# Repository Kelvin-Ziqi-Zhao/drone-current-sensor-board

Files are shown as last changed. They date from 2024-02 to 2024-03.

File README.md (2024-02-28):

# Drone Current Sensor Board
High current sensor board for battery+capacitor power supply system.
[Lastest releases](https://github.com/Kelvin-Ziqi-Zhao/drone-current-sensor-board/releases/latest)
## Components and Design
- Use **RP2040** as MCU, **INA226** as power monitor chip.
- By using **0402** components, the size of module can be greatly reduced
## More Info
- DEBUG, UART test points and IIC select are reserved, which could help us during development
- This is the theory verification PCBA module of my follow-up power system, stay tuned...
>The hardware isn't been tested, please **CHECK THE CIRCUIT** before power-on




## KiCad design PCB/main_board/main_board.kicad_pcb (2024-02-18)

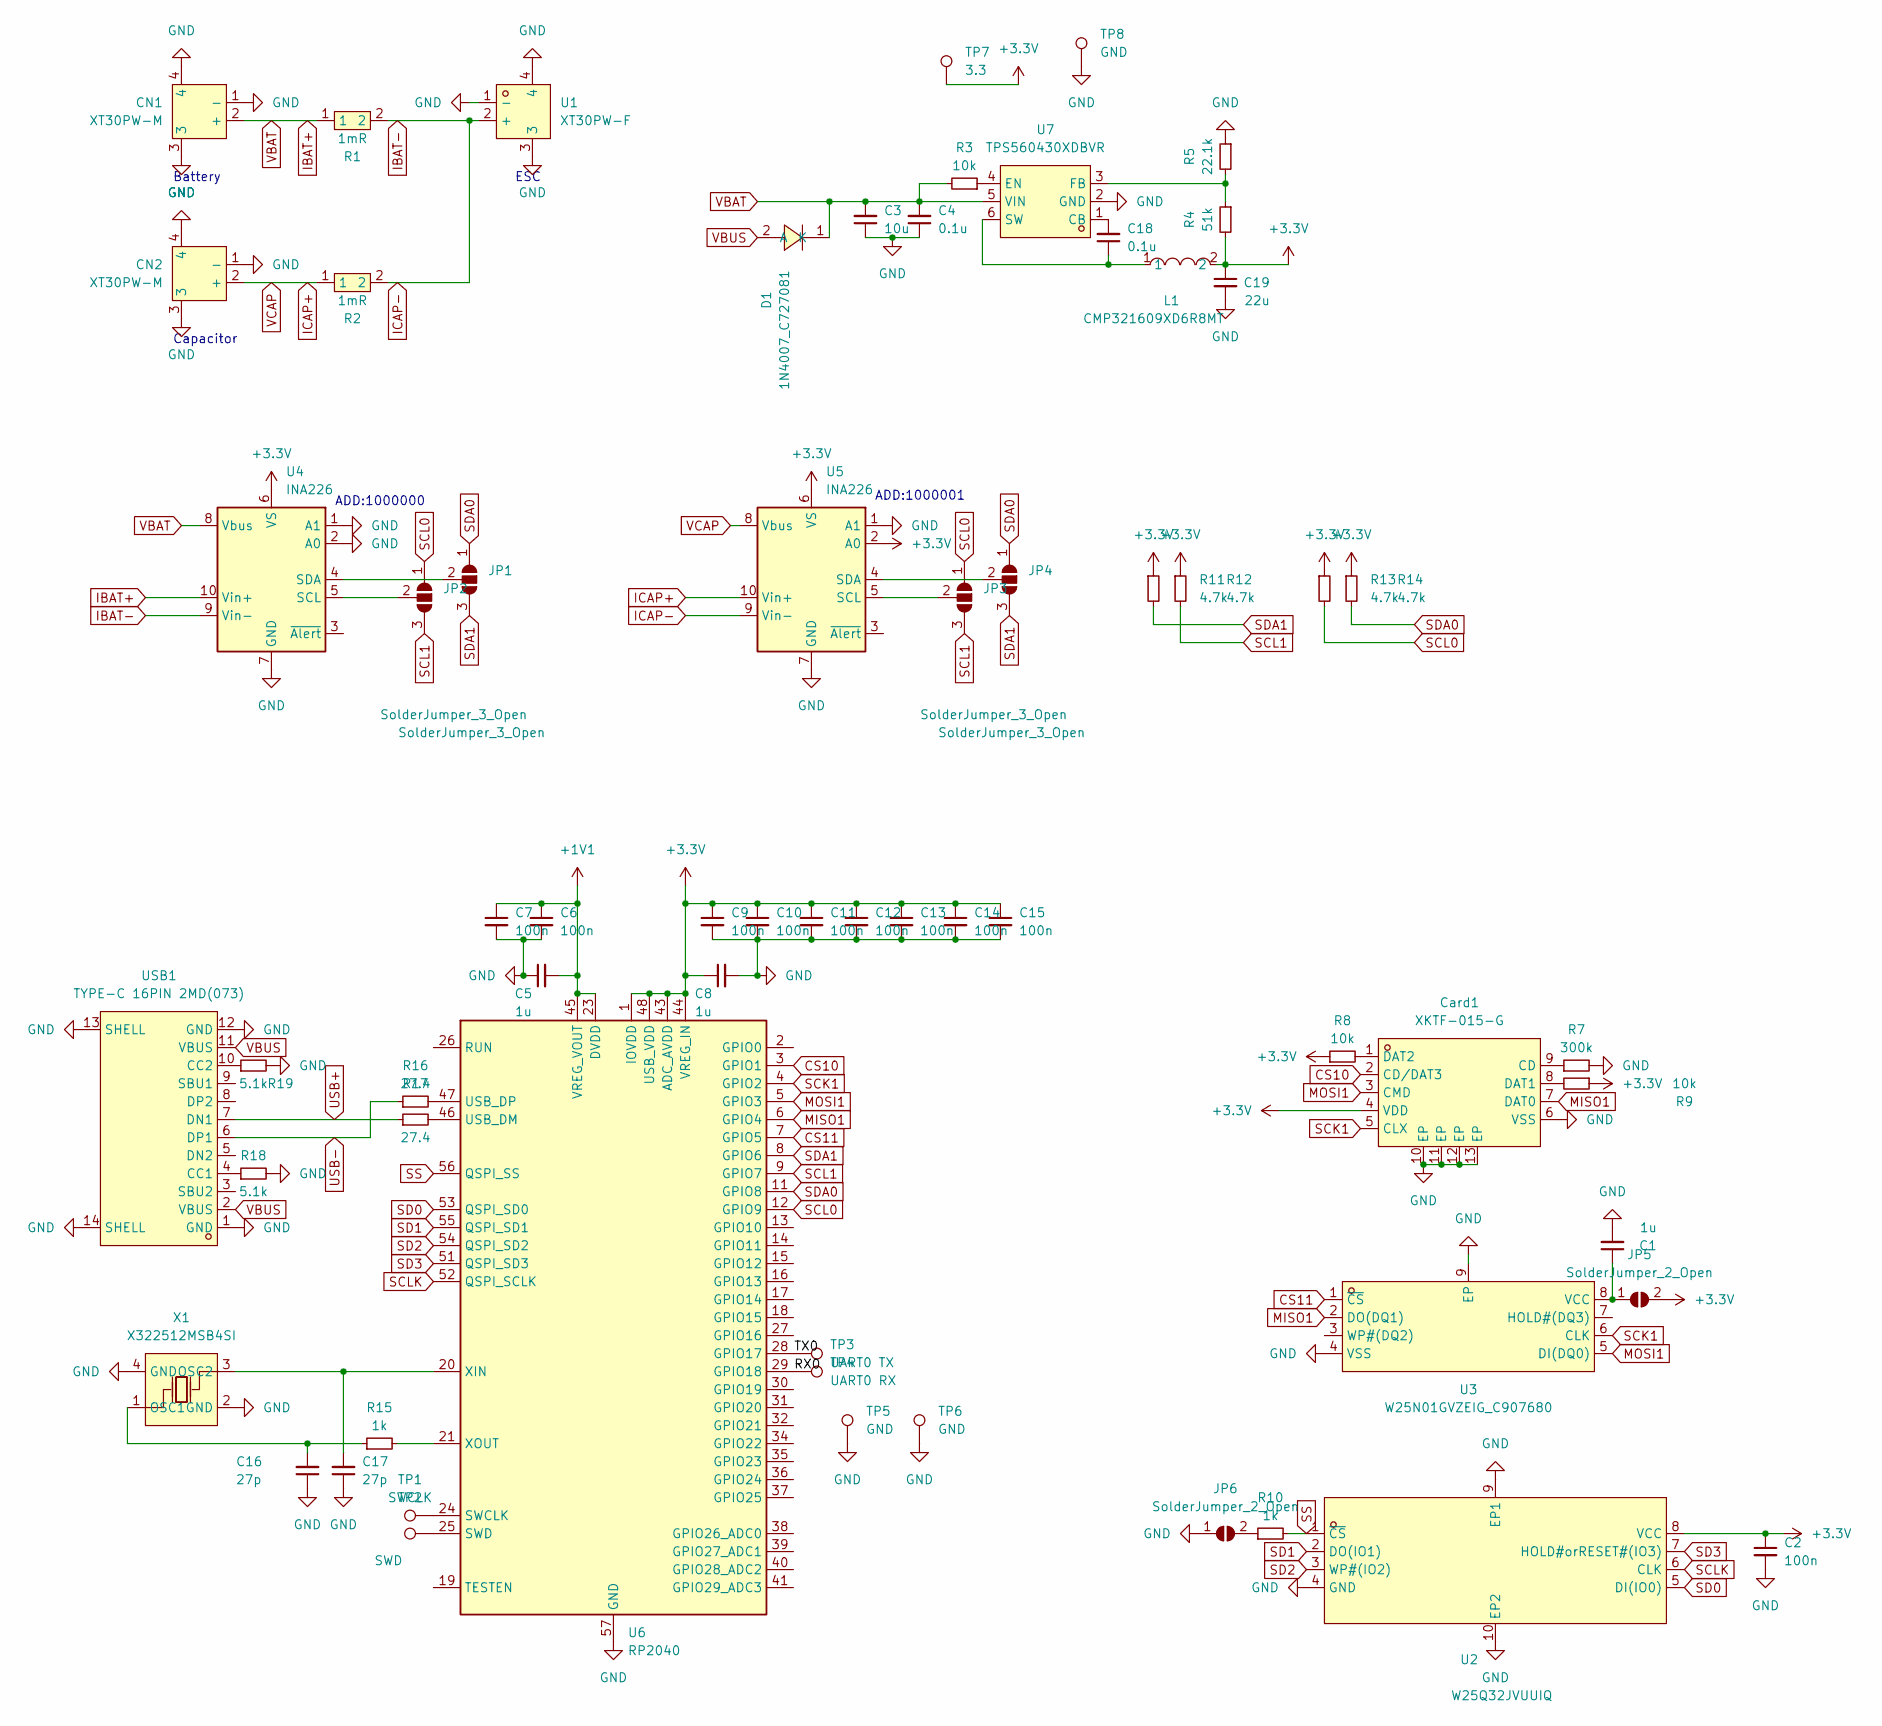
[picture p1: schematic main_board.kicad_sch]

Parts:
C1, C5, C8: 1u; C_0402_1005Metric
C2, C6, C7, C9, C10, C11, C12, C13, C14, C15: 100n; C_0402_1005Metric
C3: 10u; C_0603_1608Metric
C4: 0.1u; C_0603_1608Metric
C16, C17: 27p; C_0402_1005Metric
C18: 0.1u; C_0402_1005Metric
C19: 22u; C_0805_2012Metric
CN1, CN2: XT30PW-M; CONN-TH_XT30PW-M; LCSC Part C431092
Card1: XKTF-015-G; TF-SMD_XKTF-015-N; LCSC Part C1121874
D1: 1N4007_C727081; SMA_L4.3-W2.5-LS5.0-RD; LCSC Part C727081
JP1, JP2, JP3, JP4: SolderJumper_3_Open; SolderJumper-3_P1.3mm_Open_Pad1.0x1.5mm
JP5, JP6: SolderJumper_2_Open; SolderJumper-2_P1.3mm_Open_Pad1.0x1.5mm
L1: CMP321609XD6R8MT; L1206; LCSC Part C395031
R1, R2: 1mR; R3920; LCSC Part C5224161
R3: 10k; C_0402_1005Metric
R4: 51k; C_0402_1005Metric
R5: 22.1k; C_0402_1005Metric
R7: 300k; R_0402_1005Metric
R8, R9: 10k; R_0402_1005Metric
R10, R15: 1k; R_0402_1005Metric
R11, R12, R13, R14: 4.7k; R_0402_1005Metric
R16, R17: 27.4; R_0402_1005Metric
R18, R19: 5.1k; R_0402_1005Metric
TP1: SWCLK; TestPoint_Pad_1.5x1.5mm
TP2: SWD; TestPoint_Pad_1.5x1.5mm
TP3: UART0 TX; TestPoint_Pad_1.5x1.5mm
TP4: UART0 RX; TestPoint_Pad_1.5x1.5mm
TP5, TP6, TP8: GND; TestPoint_Pad_1.5x1.5mm
TP7: 3.3; TestPoint_Pad_1.5x1.5mm
U1: XT30PW-F; CONN-TH_XT30PW-F-1; LCSC Part C2913282
U2: W25Q32JVUUIQ; USON-8_L4.0-W3.0-P0.80-BL_WINBOND_UU; LCSC Part C2999380
U3: W25N01GVZEIG_C907680; WSON-8_L8.0-W6.10-P1.27-BL-EP; LCSC Part C907680
U4, U5: INA226; MSOP-10_L3.0-W3.0-P0.50-LS5.0-BL
U6: RP2040; QFN-56-1EP_7x7mm_P0.4mm_EP3.2x3.2mm
U7: TPS560430XDBVR; SOT-23-6_L2.9-W1.6-P0.95-LS2.8-BL; LCSC Part C524782
USB1: TYPE-C 16PIN 2MD(073); USB-C-SMD_TYPE-C-6PIN-2MD-073; LCSC Part C2765186
X1: X322512MSB4SI; OSC-SMD_4P-L3.2-W2.5-BL; LCSC Part C9002

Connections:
+1V1: C5.2, C6.1, C7.1, U6.23 (DVDD), U6.45 (VREG_VOUT), U6.50 (DVDD)
/RX0: TP4.1, U6.29 (GPIO18)
/TX0: TP3.1, U6.28 (GPIO17)
CS10: Card1.2 (CD/DAT3), U6.3 (GPIO1)
CS11: U3.1 (~CS), U6.7 (GPIO5)
IBAT-: R1.2, R2.2, U1.2 (+), U4.9 (Vin-), U5.9 (Vin-)
ICAP+: CN2.2 (+), R2.1, U5.8 (Vbus), U5.10 (Vin+)
MISO1: Card1.7 (DAT0), U3.2 (DO(DQ1)), U6.6 (GPIO4)
MOSI1: Card1.3 (CMD), U3.5 (DI(DQ0)), U6.5 (GPIO3)
unnamed: Card1.9 (CD), R7.1
unnamed: Card1.8 (DAT1), R9.2
unnamed: Card1.1 (DAT2), R8.2
unnamed: JP1.2 (C), U4.4 (SDA)
unnamed: JP2.2 (C), U4.5 (SCL)
unnamed: JP3.2 (C), U5.5 (SCL)
unnamed: JP4.2 (C), U5.4 (SDA)
unnamed: C1.1, JP5.1 (A), U3.8 (VCC)
unnamed: JP6.2 (B), R10.1
unnamed: TP1.1, U6.24 (SWCLK)
unnamed: TP2.1, U6.25 (SWD)
unnamed: R17.2, U6.46 (USB_DM)
unnamed: R16.2, U6.47 (USB_DP)
unnamed: C17.2, U6.20 (XIN), X1.3 (OSC2)
unnamed: R15.2, U6.21 (XOUT)
unnamed: C18.2, U7.1 (CB)
unnamed: R3.1, U7.4 (EN)
unnamed: R4.1, R5.2, U7.3 (FB)
unnamed: C18.1, L1.1, U7.6 (SW)
unnamed: R18.1, USB1.4 (CC1)
unnamed: R19.1, USB1.10 (CC2)
unnamed: C16.2, R15.1, X1.1 (OSC1)
SCK1: Card1.5 (CLX), U3.6 (CLK), U6.4 (GPIO2)
SCL0: JP2.1 (A), JP3.1 (A), R13.2, U6.12 (GPIO9)
SCL1: JP2.3 (B), JP3.3 (B), R12.2, U6.9 (GPIO7)
SCLK: U2.6 (CLK), U6.52 (QSPI_SCLK)
SD0: U2.5 (DI(IO0)), U6.53 (QSPI_SD0)
SD1: U2.2 (DO(IO1)), U6.55 (QSPI_SD1)
SD2: U2.3 (WP#(IO2)), U6.54 (QSPI_SD2)
SD3: U2.7 (HOLD#orRESET#(IO3)), U6.51 (QSPI_SD3)
SDA0: JP1.1 (A), JP4.1 (A), R14.2, U6.11 (GPIO8)
SDA1: JP1.3 (B), JP4.3 (B), R11.2, U6.8 (GPIO6)
SS: R10.2, U2.1 (~CS), U6.56 (QSPI_SS)
USB+: R17.1, USB1.7 (DN1)
USB-: R16.1, USB1.6 (DP1)
VBUS: D1.2 (A), USB1.2 (VBUS), USB1.11 (VBUS)

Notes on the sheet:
ADD:1000001
ESC
ADD:1000000
Battery
Capacitor

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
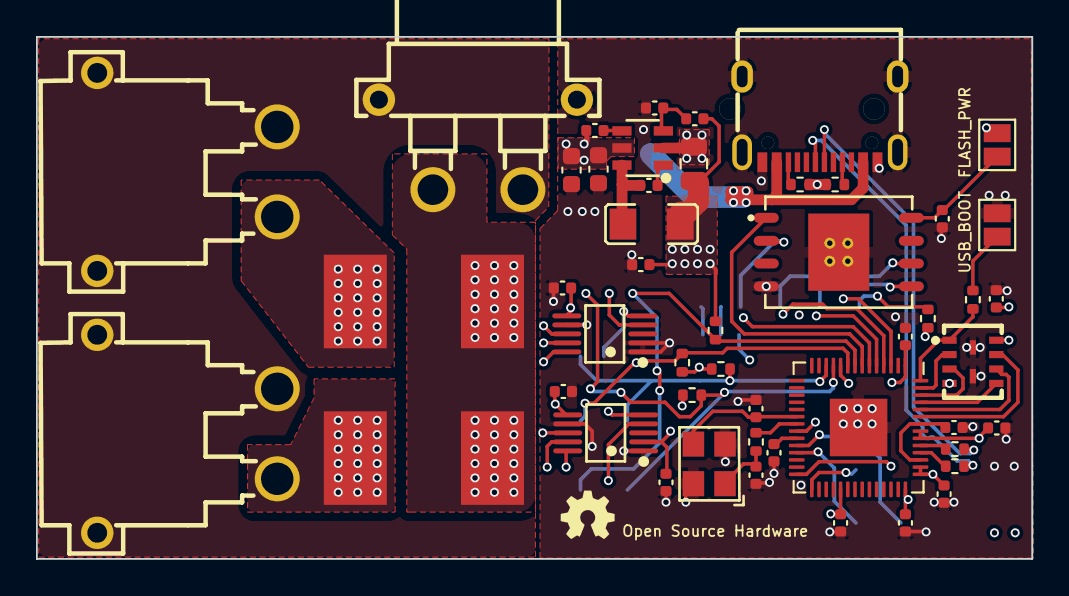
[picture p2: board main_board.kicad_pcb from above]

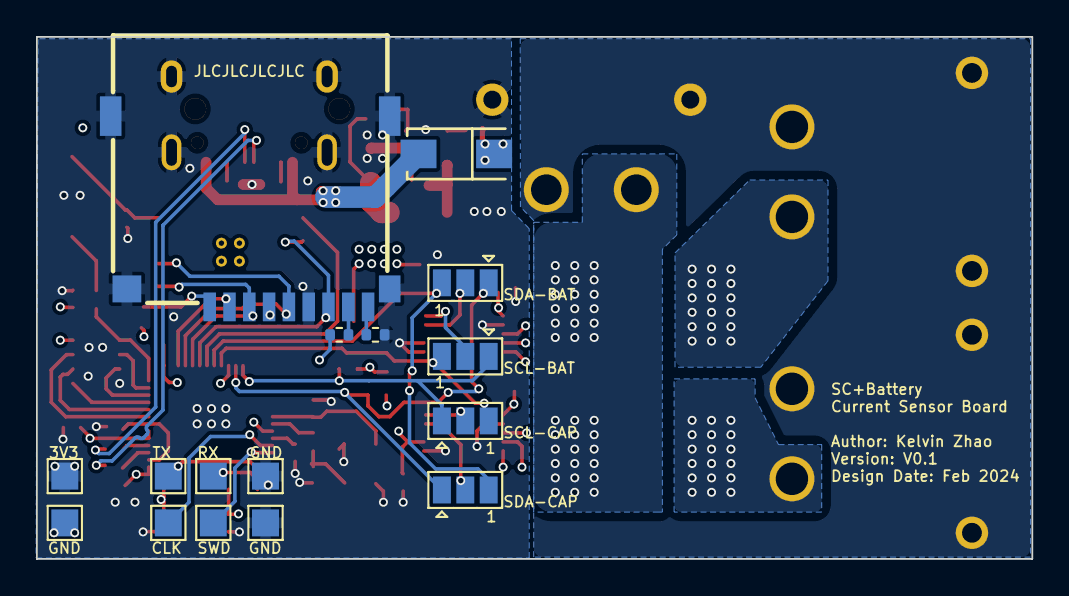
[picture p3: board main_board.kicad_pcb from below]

Board: 4 copper layers, 55.3 x 29.0 mm, 65 parts (16 on the bottom side), 48 nets.

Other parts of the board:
C4#2: 0.1u; C_0603_1608Metric

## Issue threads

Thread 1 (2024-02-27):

Wrong USB2.0 series resistance

Kelvin-Ziqi-Zhao, 2024-02-27:
The schematic and PCB design label the series resistance of 27.4R. But due to a selection mistake, a 27kR resistance has been SMT on that place. I short the wire to skip that resistance, finally it works
**SMT-BOM change required** [bom.xls](https://github.com/Kelvin-Ziqi-Zhao/drone-current-sensor-board/files/14421705/bom.xls)
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

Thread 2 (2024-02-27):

The label of 3V3 and GND test points are reversed

Kelvin-Ziqi-Zhao, 2024-02-27:
On the lower left corner (back skillscreen), the label is wrong
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

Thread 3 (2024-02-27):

Wrong UART0 pinout

Kelvin-Ziqi-Zhao, 2024-02-27:
Ref to official data sheet,  the correct UART pair is GP16-TX, GP17-RX. But in my design, I map it to GP17, GP18 :(
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

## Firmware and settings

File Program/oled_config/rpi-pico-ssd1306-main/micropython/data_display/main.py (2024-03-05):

###############################################################
# SSD1306 OLED Display I2C Tests with the Raspberry Pi Pico
# -- ADC Reading and Display of MEMS Microphone
#
# by Joshua Hrisko, Maker Portal LLC (c) 2021
#
#
# Based on the Pico Micropython repository at:
# https://github.com/raspberrypi/pico-micropython-examples/tree/master/i2c/1306oled
###############################################################
#
#
from machine import Pin, I2C, ADC
from ssd1306 import SSD1306_I2C
import framebuf,sys,time

pix_res_x  = 128 # SSD1306 horizontal resolution
pix_res_y = 64   # SSD1306 vertical resolution

i2c_dev = I2C(1,scl=Pin(7),sda=Pin(6),freq=200000)  # start I2C on I2C1 (GPIO 26/27)
i2c_addr = [hex(ii) for ii in i2c_dev.scan()] # get I2C address in hex format
if i2c_addr==[]:
    print('No I2C Display Found') 
    sys.exit() # exit routine if no dev found
else:
    print("I2C Address      : {}".format(i2c_addr[0])) # I2C device address
    print("I2C Configuration: {}".format(i2c_dev)) # print I2C params


oled = SSD1306_I2C(pix_res_x, pix_res_y, i2c_dev) # oled controller

oled.write_cmd(0xc0) # flip display to place 0,0 at lower-left corner
adc_2 = machine.ADC(2) # ADC channel 2 for input
while True:
    oled.fill(0) # clear the display
    for jj in range(pix_res_x): # loop through horizontal display resolution
        adc_pt = adc_2.read_u16() # read adc and get 16-bit data point
        plot_pt = (adc_pt/((2**16)-1))*(pix_res_y-1) # convert to OLED pixels
        oled.text('.',jj,int(plot_pt)) # update x=jj with data point
    oled.show() # show the new text and image

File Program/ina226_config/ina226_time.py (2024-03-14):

# The MIT License (MIT)
#
# Copyright (c) 2017 Dean Miller for Adafruit Industries
# Copyright (c) 2020 Christian Becker
#
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
# THE SOFTWARE IS PROVIDED "AS IS", WITHOUT WARRANTY OF ANY KIND, EXPRESS OR
# IMPLIED, INCLUDING BUT NOT LIMITED TO THE WARRANTIES OF MERCHANTABILITY,
# FITNESS FOR A PARTICULAR PURPOSE AND NONINFRINGEMENT. IN NO EVENT SHALL THE
# AUTHORS OR COPYRIGHT HOLDERS BE LIABLE FOR ANY CLAIM, DAMAGES OR OTHER
# LIABILITY, WHETHER IN AN ACTION OF CONTRACT, TORT OR OTHERWISE, ARISING FROM,
# OUT OF OR IN CONNECTION WITH THE SOFTWARE OR THE USE OR OTHER DEALINGS IN
# THE SOFTWARE.
# Edit by Kelvin Zhao
"""
`ina226`
====================================================

micropython driver for the INA226 current sensor.

* Author(s): Christian Becker

"""
# taken from https://github.com/robert-hh/INA219 , modified for the INA226 devices by
# Christian Becker
# June 2020

from micropython import const
# from adafruit_bus_device.i2c_device import I2CDevice

__version__ = "0.0.0-auto.0"
__repo__ = "https://github.com/elschopi/TI_INA226_micropython.git"

# Bits
# pylint: disable=bad-whitespace
_READ = const(0x01)

# Config Register (R/W)
_REG_CONFIG = const(0x00)
_CONFIG_RESET = const(0x8000)  # Reset Bit
# Constant bits - don't change
_CONFIG_CONST_BITS = const(0x4000)
# Averaging mode
_CONFIG_AVGMODE_MASK = const(0x0e00)
_CONFIG_AVGMODE_1SAMPLES = const(0x0000)
_CONFIG_AVGMODE_4SAMPLES = const(0x0200)
_CONFIG_AVGMODE_16SAMPLES = const(0x0400)
_CONFIG_AVGMODE_64SAMPLES = const(0x0600)
_CONFIG_AVGMODE_128SAMPLES = const(0x0800)
_CONFIG_AVGMODE_256SAMPLES = const(0x0a00)
_CONFIG_AVGMODE_512SAMPLES = const(0x0c00)
_CONFIG_AVGMODE_1024SAMPLES = const(0x0e00)

# Bus voltage conversion time
_CONFIG_VBUSCT_MASK = const(0x01c0)
_CONFIG_VBUSCT_140us = const(0x0000)
_CONFIG_VBUSCT_204us = const(0x0040)
_CONFIG_VBUSCT_332us = const(0x0080)
_CONFIG_VBUSCT_588us = const(0x00c0)
_CONFIG_VBUSCT_1100us = const(0x0100)
_CONFIG_VBUSCT_21116us = const(0x0140)
_CONFIG_VBUSCT_4156us = const(0x0180)
_CONFIG_AVGMODE_8244us = const(0x01c0)

# Shunt voltage conversion time
_CONFIG_VSHUNTCT_MASK = const(0x0038)
_CONFIG_VSHUNTCT_140us = const(0x0000)
_CONFIG_VSHUNTCT_204us = const(0x0008)
_CONFIG_VSHUNTCT_332us = const(0x0010)
_CONFIG_VSHUNTCT_588us = const(0x0018)
_CONFIG_VSHUNTCT_1100us = const(0x0020)
_CONFIG_VSHUNTCT_21116us = const(0x0028)
_CONFIG_VSHUNTCT_4156us = const(0x0030)
_CONFIG_VSHUNTCT_8244us = const(0x0038)

# Operating mode
_CONFIG_MODE_MASK = const(0x0007)  # Operating Mode Mask
_CONFIG_MODE_POWERDOWN = const(0x0000)
_CONFIG_MODE_SVOLT_TRIGGERED = const(0x0001)
_CONFIG_MODE_BVOLT_TRIGGERED = const(0x0002)
_CONFIG_MODE_SANDBVOLT_TRIGGERED = const(0x0003)
_CONFIG_MODE_ADCOFF = const(0x0004)
_CONFIG_MODE_SVOLT_CONTINUOUS = const(0x0005)
_CONFIG_MODE_BVOLT_CONTINUOUS = const(0x0006)
_CONFIG_MODE_SANDBVOLT_CONTINUOUS = const(0x0007)

# SHUNT VOLTAGE REGISTER (R)
_REG_SHUNTVOLTAGE = const(0x01)

# BUS VOLTAGE REGISTER (R)
_REG_BUSVOLTAGE = const(0x02)

# POWER REGISTER (R)
_REG_POWER = const(0x03)

# CURRENT REGISTER (R)
_REG_CURRENT = const(0x04)

# CALIBRATION REGISTER (R/W)
_REG_CALIBRATION = const(0x05)
# pylint: enable=bad-whitespace


def _to_signed(num):
    if num > 0x7FFF:
        num -= 0x10000
    return num


class INA226:
    """Driver for the INA226 current sensor"""
    def __init__(self, i2c_device, addr=0x40):
        self.i2c_device = i2c_device

        self.i2c_addr = addr
        self.buf = bytearray(2)
        # Multiplier in mA used to determine current from raw reading
        self._current_lsb = 0
        # Multiplier in W used to determine power from raw reading
        self._power_lsb = 0

        # Set chip to known config values to start
        self._cal_value = 4096
        self.set_calibration()

    def _write_register(self, reg, value):
        self.buf[0] = (value >> 8) & 0xFF
        self.buf[1] = value & 0xFF
        self.i2c_device.writeto_mem(self.i2c_addr, reg, self.buf)

    def _read_register(self, reg):
        self.i2c_device.readfrom_mem_into(self.i2c_addr, reg & 0xff, self.buf)
        value = (self.buf[0] << 8) | (self.buf[1])
        return value

    @property
    def shunt_voltage(self):
        """The shunt voltage (between V+ and V-) in Volts (so +-.327V)"""
        value = _to_signed(self._read_register(_REG_SHUNTVOLTAGE))
        # The least signficant bit is 10uV which is 0.00001 volts
        return value * 0.01 /4

    @property
    def bus_voltage(self):
        """The bus voltage (between V- and GND) in Volts"""
        raw_voltage = self._read_register(_REG_BUSVOLTAGE)
        # voltage in millVolt is register content multiplied with 1.25mV/bit
        voltage_mv = raw_voltage * 1.25
        # Return Volts instead of milliVolts
        return voltage_mv * 0.001

    @property
    def current(self):
        """The current through the shunt resistor in milliamps."""
        # Sometimes a sharp load will reset the INA219, which will
        # reset the cal register, meaning CURRENT and POWER will
        # not be available ... athis by always setting a cal
        # value even if it's an unfortunate extra step
        self._write_register(_REG_CALIBRATION, self._cal_value)

        # Now we can safely read the CURRENT register!
        raw_current = _to_signed(self._read_register(_REG_CURRENT))
        return raw_current * self._current_lsb
    
    @property
    def power(self):
        # INA226 stores the calculated power in this register        
        raw_power = _to_signed(self._read_register(_REG_POWER))
        # Calculated power is derived by multiplying raw power value with the power LSB
        return raw_power * self._power_lsb
# Example calculations for calibration register value, current LSB and power LSB
# 1. Assuming a 100milliOhm resistor as shunt
# RSHUNT = 0.1
#
# 2. Determine current_lsb
# Assuming a maximum expected current of 3.6A
# current_lsb = MaxExpected_I / (2^15)
# current_lsb = 3.6A / (2^15)
# current_lsb = 0.0001098632813
# -> Rounding to "nicer" numbers:
# current_lsb = 0.0001
#
# 3. Setting the power LSB
# power_lsb = 25 * current_lsb
# power_lsb = 25 * 0.0001
# power_lsb = 0.0025
#
# 4. Determine calibration register value
# cal_value = 0.00512 / (RSHUNT * current_lsb)
# cal_value = 0.00512 / (0.1 * 0.0001)
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

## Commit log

2024-02-12 Local file update
    [main_board.kicad_pcb, main_board.kicad_sch]
2024-02-12 Create pcb layout
    [main_board.kicad_pcb]
2024-02-12 Fundamental pcb layout
    [main_board.kicad_pcb]
2024-02-12 Change INA226 connection
    [main_board.kicad_sch]
2024-02-12 add PCB outline, redesign power component
    [main_board.kicad_pcb]
2024-02-12 basic layout complete
    [main_board.kicad_pcb]
2024-02-12 stage pull
    [main_board.kicad_pcb]
2024-02-13 Change lib to relative path
    [main_board.kicad_pcb]
2024-02-14 Add EEPROM to mcu; Change R and C to 0402
    [main_board.kicad_pcb, main_board.kicad_sch]
2024-02-14 Fundamental layout complete
    [main_board.kicad_pcb]
2024-02-14 Change IIC0, IIC1 and SPI connection GPIO
    [main_board.kicad_pcb, main_board.kicad_sch]
2024-02-14 Complete SPI Flash and part of decouple capacitor layout
    [main_board.kicad_pcb, main_board.kicad_sch]
2024-02-14 Complete INA226 IIC trace
    [main_board.kicad_pcb]
2024-02-14 Complete high current trace
    [main_board.kicad_pcb, main_board.kicad_sch]
2024-02-14 Complete VBUS trace; Adjust Flash position
    [main_board.kicad_pcb]
2024-02-16 Complete USB DP routing
    [main_board.kicad_pcb, main_board.kicad_sch]
2024-02-16 PCB route complete
    [main_board.kicad_pcb]
2024-02-16 Optimize ref to DCR
    [main_board.kicad_pcb]
2024-02-16 DRC Check complete
    [main_board.kicad_pcb]
2024-02-16 Place text for test point; Disconnect a ground error connection
    [main_board.kicad_pcb, main_board_bom.csv]
2024-02-16 Thicker the single ground connection
    [main_board.kicad_pcb]
2024-02-16 Ready to JLC
    [main_board.kicad_pcb]
2024-02-17 Change LDO to BUCK converter
    [main_board.kicad_pcb, main_board.kicad_sch]
2024-02-17 Ready for JLC for second time
    [main_board.kicad_pcb]
2024-02-17 Remove extra current carrier
    [main_board.kicad_pcb]
2024-02-17 Add Custom ID
    [main_board.kicad_pcb]
2024-02-17 Change vias drills to 0.3/0.5mm
    [main_board.kicad_pcb]
2024-02-18 Change INA226 package for SMT
    [main_board.kicad_pcb, main_board.kicad_sch]
2024-02-28 change release tag to v0.1.0
    [bom.xls, positions.csv]
2024-03-04 import rpi-pico-ssd1306
